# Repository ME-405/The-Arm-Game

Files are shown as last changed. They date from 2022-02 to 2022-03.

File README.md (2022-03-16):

# The Arm Game

Jacob Bograd, Nicholas De Simone, Horacio Albarran

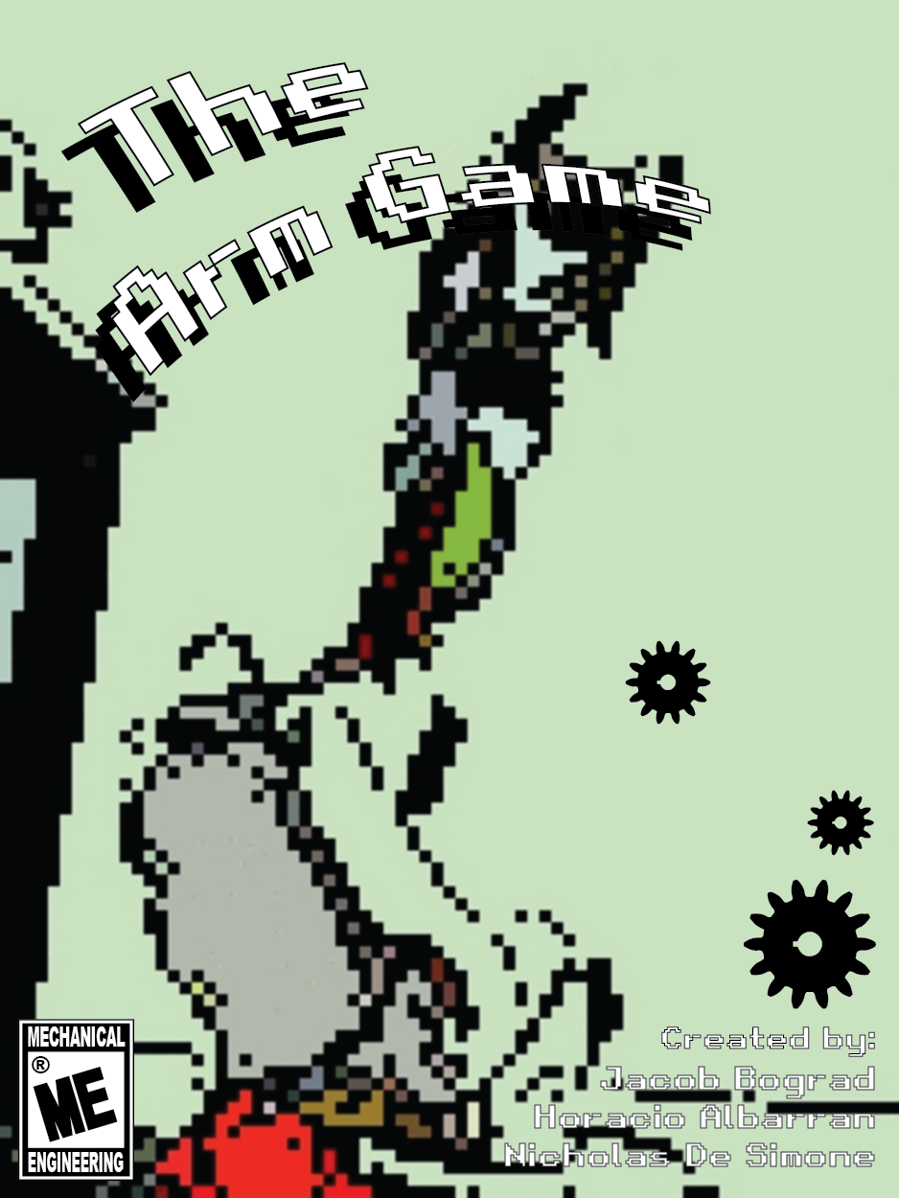
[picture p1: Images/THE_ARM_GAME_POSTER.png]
Poster


## Introduction

Our 3D-printed robotic arm is manipulated using a game controller, where the goal in using the arm is to grab a ping-pong ball and drop it through the "catching tables". The game controller communicates to the host computer over a library obtained through GitHub, and the PC interprets the controller inputs as desired end effector locations and sends them to a l476RG Nucleo. The Nucleo reads the given input arguments as x,y, and z-coordinates and transforms them into respective motor PWM values, which correspond to necessary angular positions for the servos. The Nucleo also sends the DC motor's encoder values back to the computer. All of the calculations are handled on the computer side, such that the Nucleo only sets PWM values for the respective motor and/or servos in order to get to the specified position for the claw at the end of the robotic arm. 

## Demonstration Video
The following video shows the functioning mechanism: 

https://user-images.githubusercontent.com/97562028/157779387-043f62d6-f68d-46a5-b4d3-32e55e5b0366.mp4

## Documentation and Software Design

There are ten .py files for the micro-controller side of the controller program. Such files allow for closed loop control of the used motor as well as providing with the required calculations in order to operate the arm, elbow, and clamping mechanism of the links.  
On the other hand, there is one required file on the computer side in order to open the console for the game controller to be used and provide with the desired x,y, and z-coordinates of the desired point in space where the claw must be located in order to grab the desired object, in this case, a ping-pong ball.
For further information, please refer to the following link for any documentation regarding "The Arm Game" project:

https://me-405.github.io/The-Arm-Game/

## Wiring Key
### Power
Red electrical Tape - 12V Motor \
Yellow electrical Tape - 7V Servo \
Green Electrical Tape  - 5V MicroServo \
Blue with Green - GND \
Black with Yellow - 7V

### Data
White - Servo0 \
Blue - Servo1 \
Black - Servo2\
Yellow - Servo3

### Data Nucleo Pins
PA5 - Servo0 \
PA6 - Servo1 \
PA7 - Servo2\
PC7 - Servo3

# Bill of materials

| Qty. | Part | Source | Est. Cost |
|:----:|:---|:---|:---:|
|  1 | Pittperson Gearmotors | ME405 Tub | - |
|  1 | l476RG Nucleo with Shoe | ME405 Tub | - |
|  2 | MG996R Servos[Package] | Amazon | 26.99 |
|  2 | SG90 Micro Servo [Package] | Amazon | 10.69 |
|  1 | Arms, Base, & Waist [3-D printed] | Bonderson's Building  | - |
|  1 | Game Controller [PS5 controller] | Jacob's Toolbox | 59.99 |
|  1 | Gear | 3-D printed | - |
| 10+  | Assorted metric bolt and nuts | Ace Hardware | - |
|  1 | Ping-Pong ball | Found | - |

# Gallery
## System Assembly
The following images show an overview of the arm mechanism:

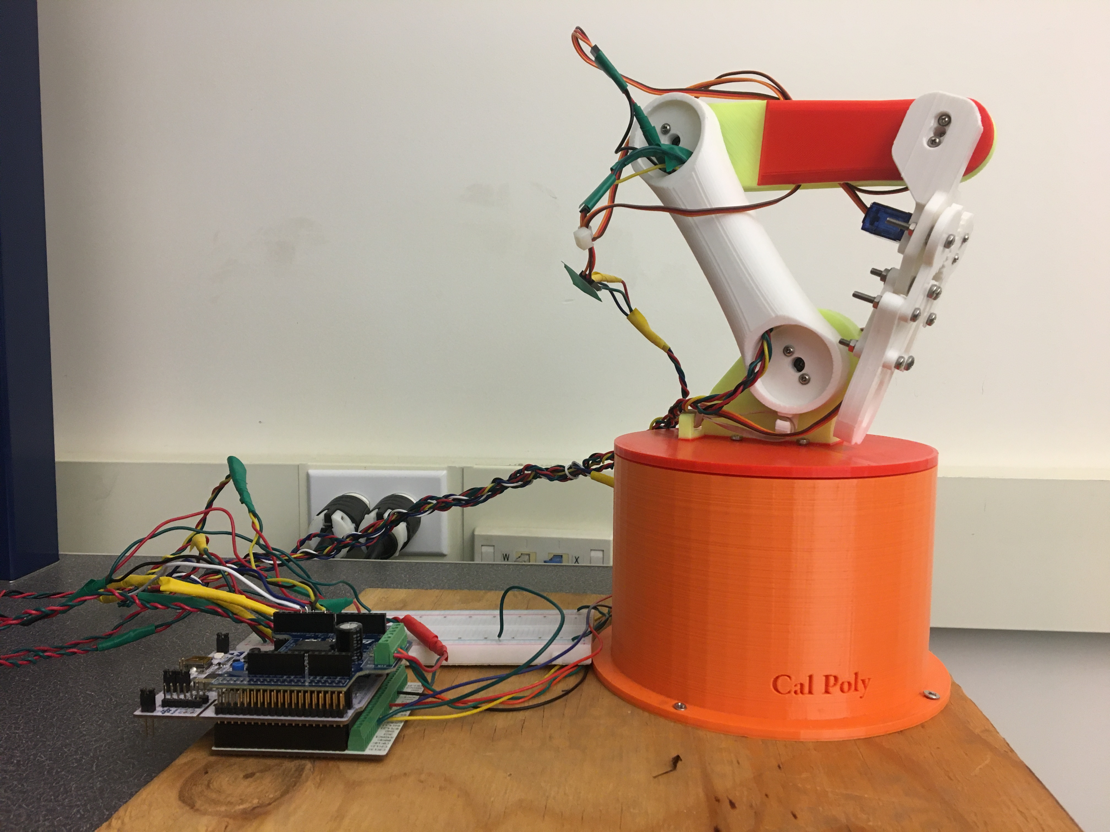
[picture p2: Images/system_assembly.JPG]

Figure 1: Overall system assembly. Complete arm mechanism shown to the right and microcontroller stack to the left. 

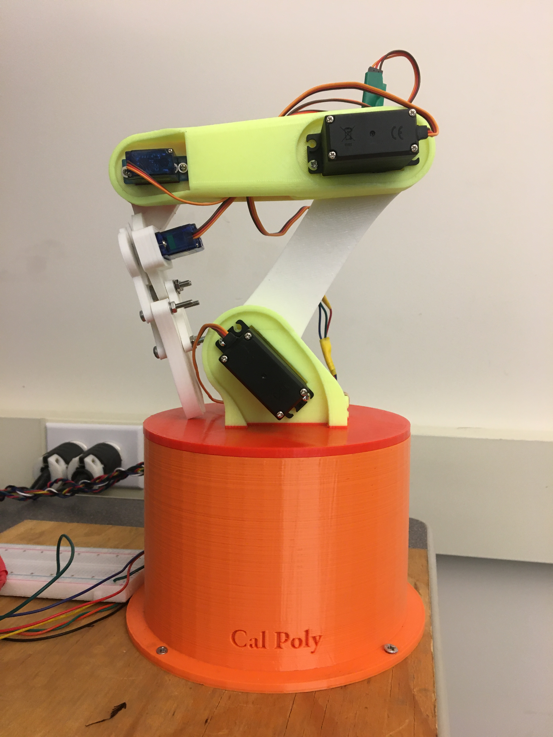
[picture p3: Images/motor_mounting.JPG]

Figure 2: Servo locations. 

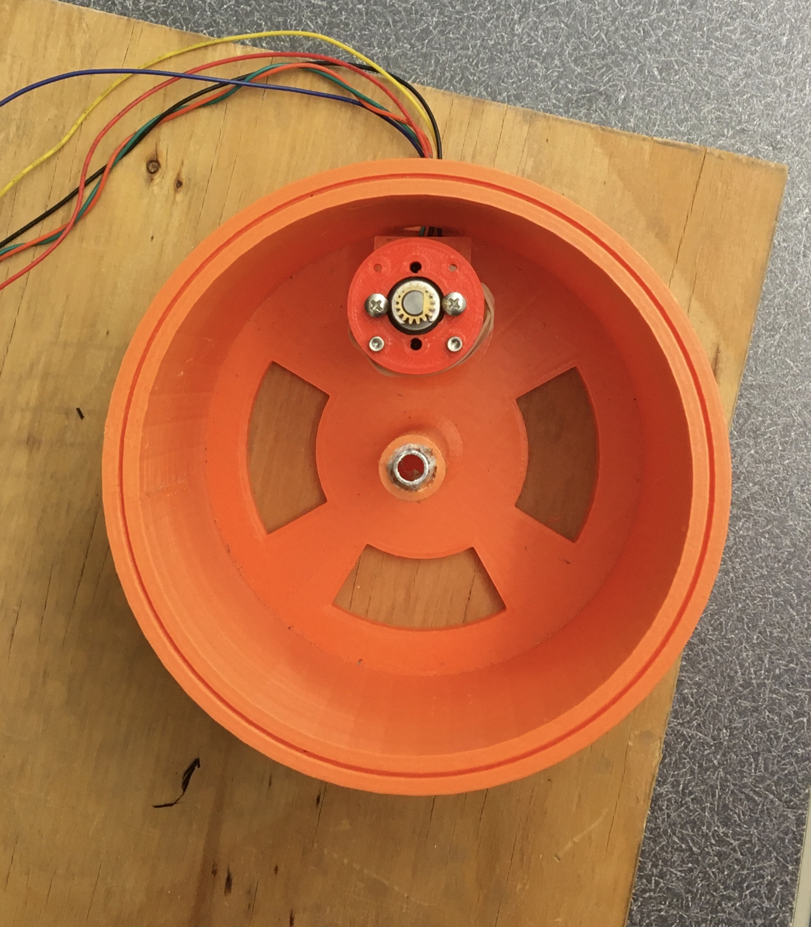
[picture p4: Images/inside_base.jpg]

Figure 3: Open-view of the base. Note (1) the internal vertically-mounted DC-motor, which mates to the waist's gear with a 7:1 gear ratio, and (2) the center-most shaft for mounting of the arm/waist assemblies to the base.

## Catching Table Sketch
The following model was constructed to be able to catch the ping-pong ball in an effective manner.
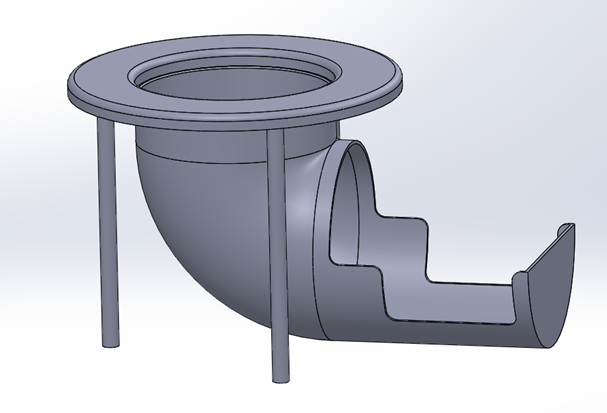
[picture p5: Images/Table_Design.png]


Figure 4: Model used for the Table hardware.

# Testing
System testing allowed us to observe physical constraints of the assembly and control them accordingly.
To begin, each component of the systems was tested individually (i.e. unique PWM signals were sent to each motor to ensure they behaved appropriately). 
An important component to testing became linkage alignment; we fixed the printed arms to the servo end effectors at strategic starting positions, such that each 
0-180 degree servo position produces desirable arm orientations.

We would like to note that communicating to a second terminal through the upper-most UART port on the microcontroller stack was a helpful feature in testing, as it allowed
for viewable debug statements from the Nucleo while busy sending actuation locations over its bottom-most USB-VCP port.
The mechanism did ultimately have undesirable behavior, which may be observed at length in the "Recommendations" section.

## Recommendations
It is important to note that, in our attempt to compute linkage angles according to a desired end effector location, our use of inverse kinematics control sometimes
produced unfavorable singularities in the arm's motion. Likely, our source of error stemmed from our application of a 2 degree-of-freedom, 2-link inverse kinematic
model to our controller, whereas, in practice, our robot arm has 3 degrees-of-freedom (not accounting for the gripper's pitch or close, as these were not included in our 
defined end effector location, i.e. the "end effector location" refers to the gripper wrist). Subsequent research into this error has suggested that the computation of 
linkage angles from an inputted end effector location may result in two unique orientations of the robot arm- either in the "elbow up" or "elbow down" configuration- at 
times producing undesired behavior. For example, when transistioning between specific points in space, the arm underwent rapid transition from "elbow up" to 
"elbow down", sometimes crashing the bot into the table or other times producing large inertial moments on the gripper assembly, causing it to snap at the end of its motion.
Possible solutions may include (1) proper consideration of and selection between the two unique orientation solutions found by our motor controller/kinematic solver scripts,
or (2) implementation of alternative controller methods, such as the Newton Raphson. The Newton Method may be more suited for our system because the arm has more than two DOF's.

We also found limits on the arms actuation in the radial direction due to insufficient fixturing/support at the base of the arm. Resultant undesired behavior included the arm
"jumping off" its orange base when actuating at a large radial distance (close to the length of both arms extended horizontally). Possible solutions include (1) fixing the
gear (currently attached on the undermost surface of the revolving waist) to both the orange base and the revolving waist, or (2) attaching physical masses to the
waist to counteract force moments when actuating in the downward direction.

It would also be recommended to obtain servos with higher output torque, as the 7V servos had difficulty sustaining the mechanism's weight. The microservos were able to
control gripper pitch and close without issue.

## Structural Components
Please refer to the following link for the 3D-printed structual components:

https://github.com/ME-405/The-Arm-Game/tree/main/Hardware_Components

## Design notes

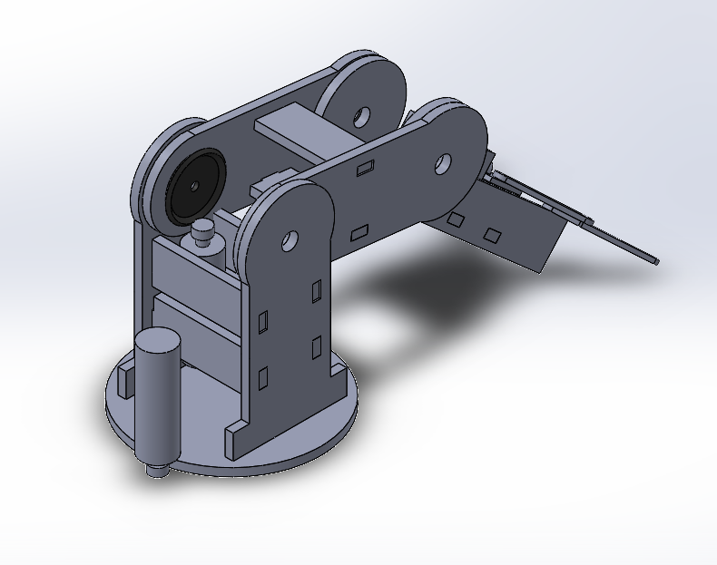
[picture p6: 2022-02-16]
docs/rough_model_back.png

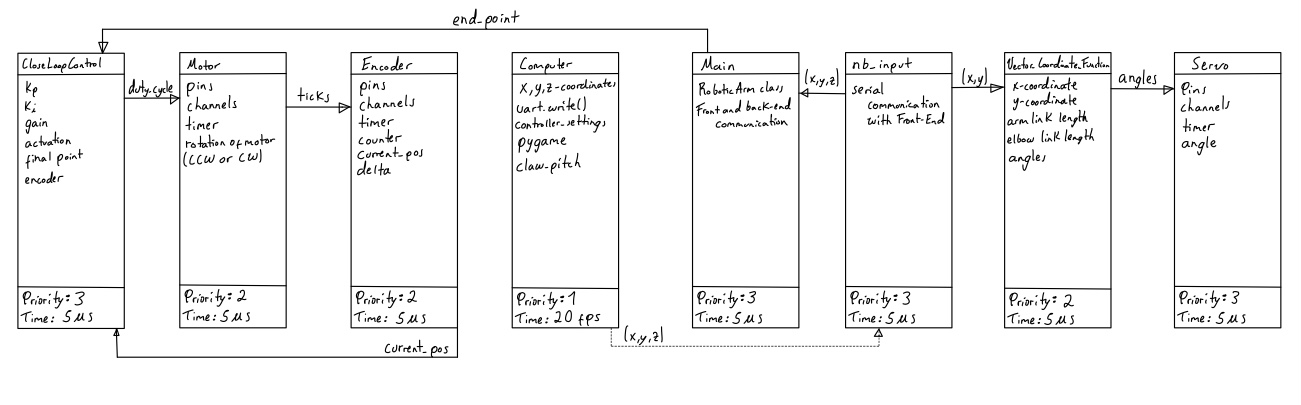
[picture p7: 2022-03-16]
docs/Task_Diagram.png

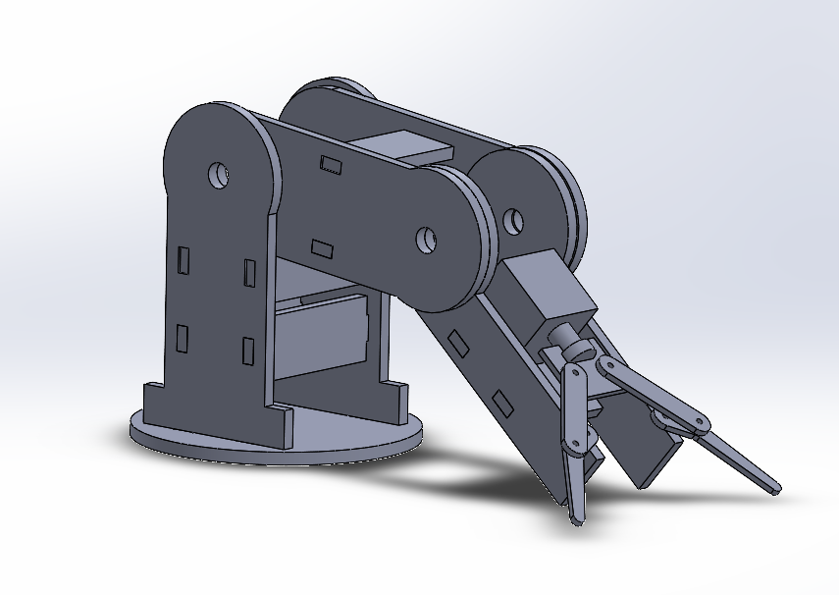
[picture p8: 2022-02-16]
Images/rough model.png

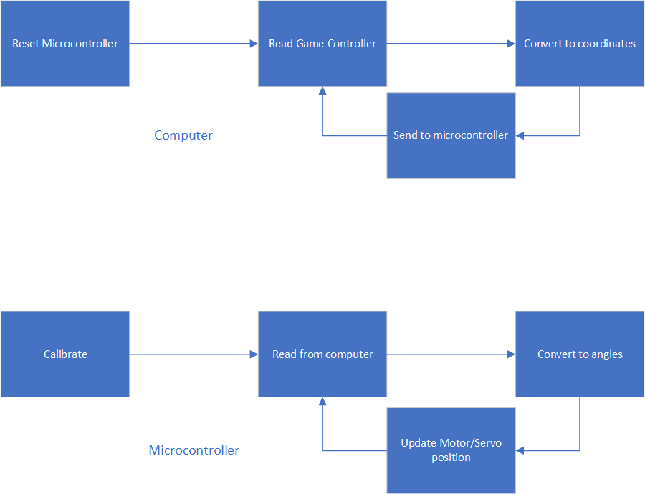
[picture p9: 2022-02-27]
Images/intinal_fsm.png

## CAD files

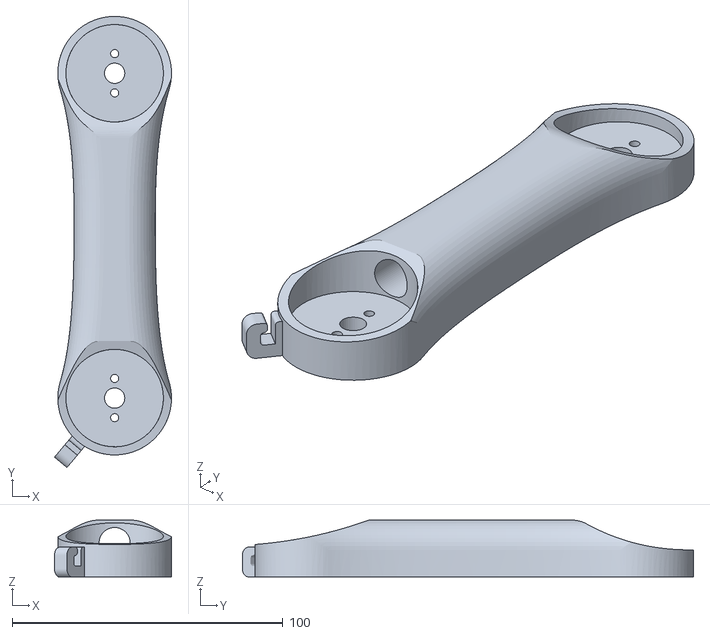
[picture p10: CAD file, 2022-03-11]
Hardware_Components/Arm 01.STL
43.2 x 166.7 x 21.0

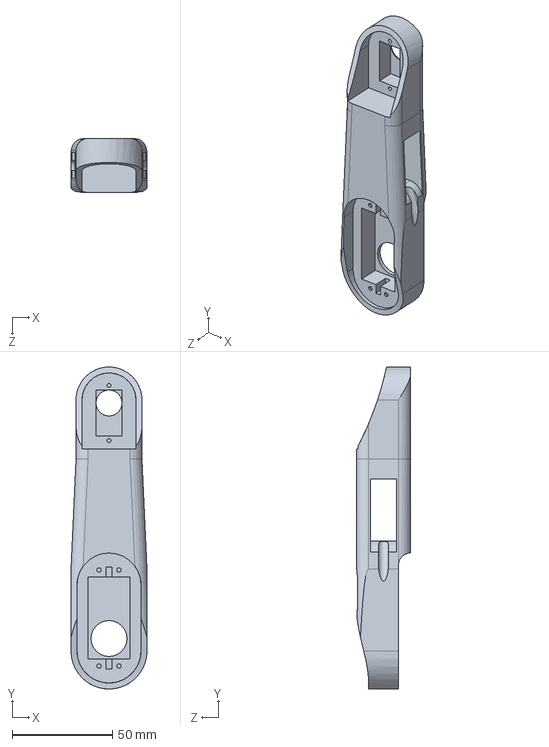
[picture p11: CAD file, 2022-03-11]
Hardware_Components/Arm 02 V4.SLDPRT
38.0 x 161.0 x 27.0 mm

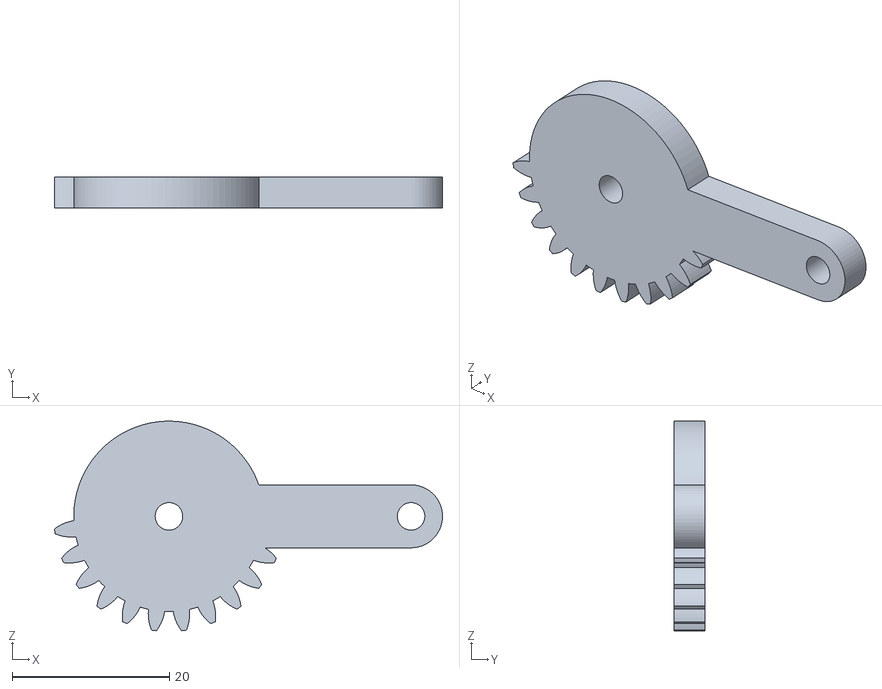
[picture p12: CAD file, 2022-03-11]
Hardware_Components/gear1.STL
49.3 x 4.00 x 26.6

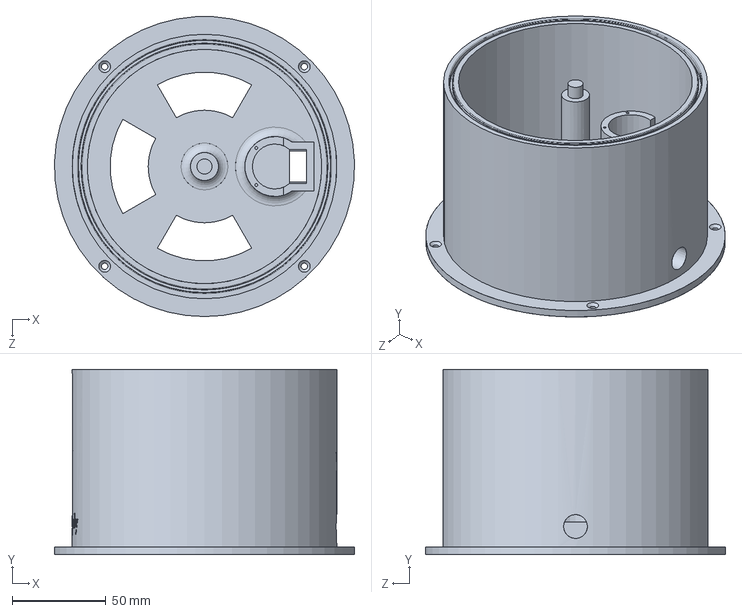
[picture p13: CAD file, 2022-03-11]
Hardware_Components/Base V3.SLDPRT
159.9 x 98.8 x 160.0 mm

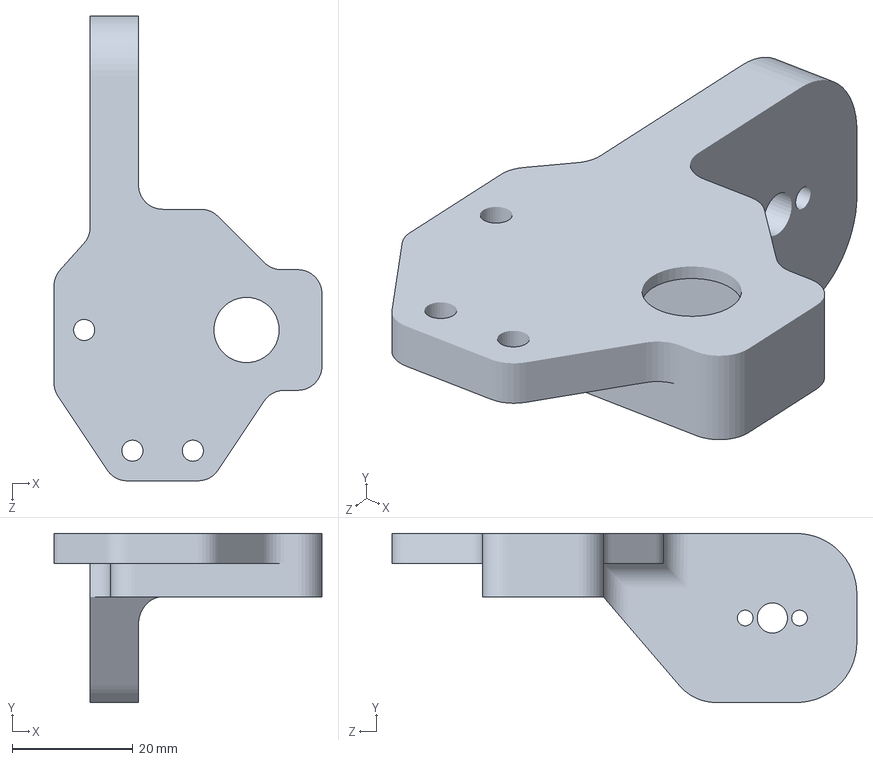
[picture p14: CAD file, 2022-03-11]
Hardware_Components/Gripper base.SLDPRT
44.4 x 28.0 x 77.0 mm

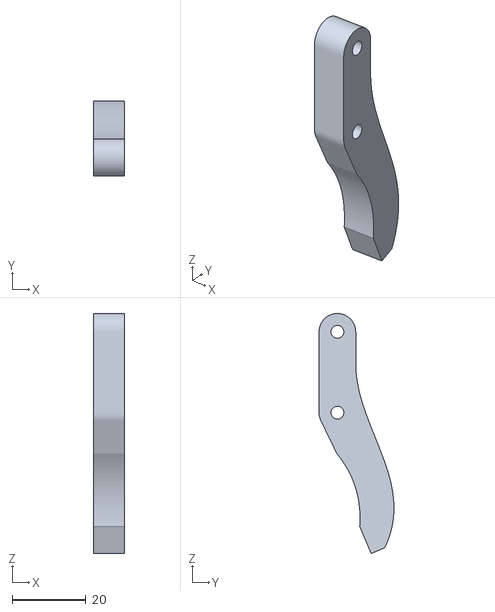
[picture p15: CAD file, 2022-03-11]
Hardware_Components/Gripper 1.STL
8.50 x 20.4 x 65.3

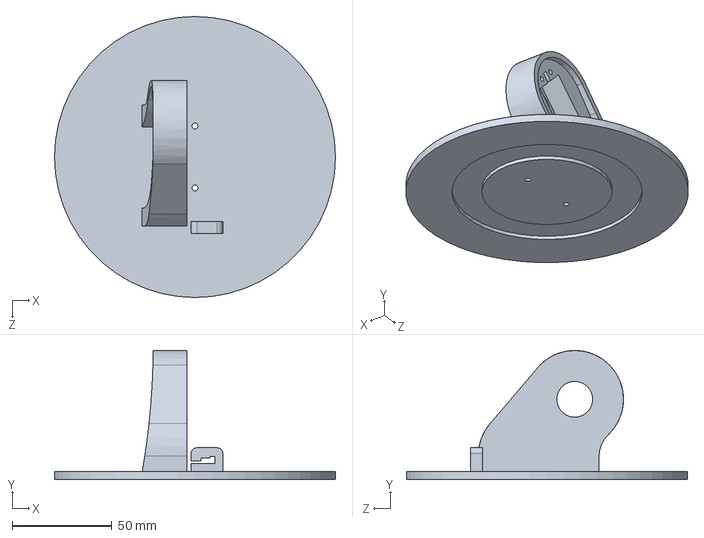
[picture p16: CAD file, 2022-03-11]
Hardware_Components/Waist V5.SLDPRT
141.0 x 64.8 x 141.0 mm

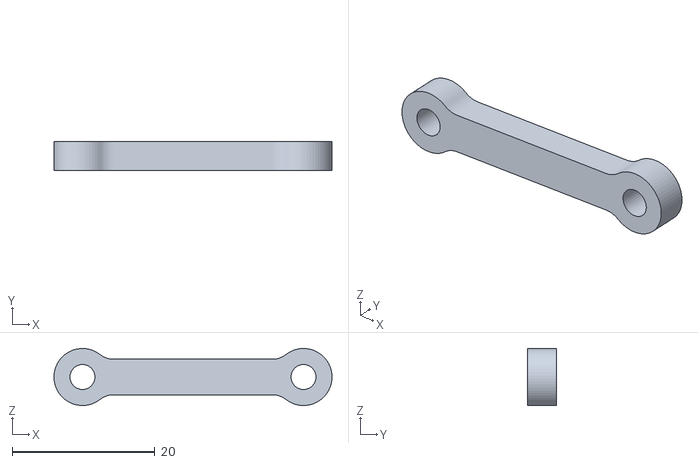
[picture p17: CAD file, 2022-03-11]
Hardware_Components/grip link 1.STL
39.0 x 4.00 x 8.00

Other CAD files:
Hardware_Components/gear2.STL

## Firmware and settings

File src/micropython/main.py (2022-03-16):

'''!
@file main.py
@details This is the main file for the Micropython side of this project. It contains the FSM that controls the whole system.
'''

#  Importing libraries and classes
from pyb import USB_VCP
from nb_input import NB_Input
from servo import Servo
from Motor import MotorDriver
from encoder import Encoder
from closedLoopControl import ClosedLoopController as ClosedLoop
from pyb import UART
from Vector_Coordinate_Function import ElArAngles
import pyb
import gc
import cotask
import task_share
import math

INPUTINTERVAL = 10

DEFAULTANGLE = 60  # the default angle


# Instantiated the objects for the servos


def main():
    '''!
    @breif This is the main function that the MCU runs  whenever it is restarted
    '''
    # start by creating a share and queue
    arm = RoboticArm()  # make a new robotic arm

    # I am not sure if the share and queue are needed
    share = task_share.Share('h', thread_protect=False, name="Share")
    queue = task_share.Queue('L', 16, thread_protect=False, overwrite=False,
                             name="Queue")
    per_val = 5
    read_task = cotask.Task(arm.read_uart, name='read', priority=1, period=per_val, profile=False, trace=False)
    calculate_task = cotask.Task(arm.calculate_parameters, name='calculate', priority=2, period=per_val, profile=False,
                                 trace=False)
    update_task = cotask.Task(arm.update_parameters, name='update', priority=2, period=per_val, profile=False,
                              trace=False)
    clc_task = cotask.Task(arm.clc.control_algorithm, name='clc', priority=3, period=per_val, profile=False,
                           trace=False)
    # append all the tasks to the task list
    read = arm.read_uart()
    calculate = arm.calculate_parameters()
    update = arm.update_parameters()
    clc = arm.clc.control_algorithm()
    cotask.task_list.append(read_task)
    cotask.task_list.append(calculate_task)
    cotask.task_list.append(update_task)
    cotask.task_list.append(clc_task)

    gc.collect()
    # run the garbage collector

    # run the scheduler
    print("hello Computer")
    while True:
        # next(read)
        # print("calculating")
        # next(calculate)
        # print("Updating")
        # next(update)
        # print("clc")
        # print(f"MCU DEBUG: error: {arm.clc.send_error}, actuation: {arm.clc.send_actuation}, current pos {arm.clc.encoder.current_pos}, final pos {arm.clc.final_point}")
        # for i in range(1, 10):
        # next(clc)
        # Everything above this is DEBUG
        cotask.task_list.pri_sched()  #Grab another cotask
    print("Look All Done")  # DEBUG, this will not happen


class RoboticArm:
    def __init__(self, uart_channel=2, baudrate=115200):
        '''!
        @brief TODO
        @details TODO
        @param uart_channel     This is the uart channel that we will be using for communication
        @param baudrate         This is the baudreate that we will be using for communication
        TODO update the doxygen from @param
        @param self.uart        This is the uart channel that we will be using for communication with the host machine
        @param self.clc         This is the close loop controller for the base
        @param self.command     This is the raw command taken from the host computer, it will be processed into angles and positions at a later date
        @param self.angles      This is a list that contains all of the angles for the servos to go to
        @param self.endpoint    This is the updated encoder endpoint for the base
        @param self.new_values  This is a boolean to determine if we need to update the parameters
        @param self.mail        This is a boolean to determine if we have new mail from the computer
        '''

        # Instantiated object for the encoder as well as timer,
        encoderPin1 = pyb.Pin(pyb.Pin.board.PB6)
        encoderPin2 = pyb.Pin(pyb.Pin.board.PB7)
        EncTimer1 = 4
        EncoderDriver = Encoder(encoderPin1, encoderPin2, EncTimer1, 1, 2)

        # Instantiated the objects for the motor
        motorEnable1 = pyb.Pin(pyb.Pin.board.PC1, pyb.Pin.IN, pyb.Pin.PULL_UP)
        motor1Pin1 = pyb.Pin(pyb.Pin.board.PA0, pyb.Pin.OUT_PP)
        motor1Pin2 = pyb.Pin(pyb.Pin.board.PA1, pyb.Pin.OUT_PP)
        motorTimer = pyb.Timer(5, freq=20000)
        Motor = MotorDriver(motorEnable1, motor1Pin1, motor1Pin2, motorTimer, 1, 2)

        # Conditionals for the USB coms
        self.serial_stream = USB_VCP()
        self.nb_in = NB_Input(self.serial_stream, echo=False)

        # now setup all of the class variables


        self.clc = ClosedLoop(EncoderDriver, Motor)  # make a new closed loop controller
        # self.command = [1, 0.1, 0.1, 100, 60]  #DEBUG
        self.command = None  # set the command to nothing

        # make the 4 servo objects, the pins are hard-coded
        # The setup for the pins might not be correct
        self.servo0 = Servo(pyb.Pin(pyb.Pin.board.PA5), 2, 1)  # The lower arm servo
        self.servo1 = Servo(pyb.Pin(pyb.Pin.board.PA6), 3, 1)  # The middle arm servo
        self.servo2 = Servo(pyb.Pin(pyb.Pin.board.PA7), 3, 2)  # The upper arm servo
        self.servo3 = Servo(pyb.Pin(pyb.Pin.board.PC7), 8, 2)  # The claw servo
        self.angles = [DEFAULTANGLE, DEFAULTANGLE, DEFAULTANGLE, DEFAULTANGLE]  # set all of the angles to default
        self.endpoint = DEFAULTANGLE  # Set the default endpoint
        self.new_values = False  # we do not have any new values to read
        # self.mail = True # DEBUG
        self.mail = False  # we do not have any mail from the computer
        self.VCF = ElArAngles()  # make the Vector Coordinate Function
        self.conversion_factor = 319  # The conversion factor from angle to encoder ticks

    # TODO ADD DOXY
    def read_uart(self):
        while True:
            if self.nb_in.any():
                # if True:
                # if self.uart.any():  # check if there is something in the pipeline
                command_string = self.nb_in.get().split(',')  # read in the command and split on ,
                self.command = [float(coordinate) for coordinate in command_string]  # convert the string list to float
                print("ACK")  # we acknowledge
                self.mail = True  # we have some mail to sort through
            else:
                # print("No Mail") # DEBUG
                self.mail = False  # we have no new mail
            yield 0  # let another task have its turn in the spotlight

    # TODO ADD DOXY
    def calculate_parameters(self):
        # The format is X,Y,Z,CLAW PITCH, CLAW CLOSE
        while True:
            if self.mail:  # only calculate parameters if there is something that we need to do
                #  Get the base angle
                #  Ange = arctan(y/x)
                radians = math.atan2(self.command[1], self.command[0])  # get the angle in radians
                self.endpoint = radians * self.conversion_factor * 180 / math.pi  # convert the angle to encoder ticks
                # radius = math.sqrt(self.command[0]**2 + self.command[1]**2)
                self.VCF.set_angles(self.command[1], self.command[2])  # update the VCF with the new angles
                self.VCF.run()  # Have the VCF calculate the new angles

                # Get the angles for the 4 servos
                self.angles[0] = self.VCF.tetha1
                self.angles[1] = 180 - (self.VCF.tetha2 + 90)  # The servo is backwards
                # print(self.angles[1])  # DEBUG
                # The claw close and pitch are given as angles

                self.angles[2] = 180 - self.command[3]  # get the claw pitch value
                self.angles[3] = self.command[4]  # get the claw close value
                self.new_values = True
            yield 0  # send it back for another task to take over

    def update_parameters(self):
        while True:
            if self.new_values:
                # update the servo angles
                self.servo0.SetAngle(self.angles[0])
                self.servo1.SetAngle(self.angles[1])
                self.servo2.SetAngle(self.angles[2])
                self.servo3.SetAngle(self.angles[3])
                # update the base endpoint
                self.clc.final_point = self.endpoint
                # print(f"angle0 {self.angles[0]} angle1 {self.angles[1]} angle2 {self.angles[2]} angle3 {self.angles[3]}")
            else:
                manual_breathing = 1  # you are now manually breathing
            yield 0  # let another function have its turn

    # this is just a simple pass-through to run the clc update
    def clc_passthrough(self):
        self.clc.control_algorithm()

    def zero_encoder(self):
        '''!
        @brief This resets the encoder value in the clc to 0, for use in case of a failure and without a hardware reset
        '''
        self.clc.encoder.zero()


# Dunder method to run the function when the name of the file is main,
if __name__ == '__main__':
    main()

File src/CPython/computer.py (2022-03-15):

import pygame
import serial
import time


# constants
XLIMIT = 4.65 * 2
YLIMIT = 4.65 * 2
ZLIMIT = 4.65 * 2
debug = False
ACK = True
try:
    uart_to_micro = serial.Serial(port='COM5', baudrate=115200, timeout=0)
    # reset the Microcontroller
    uart_to_micro.write(b'\x03')  # send Ctr+C
    time.sleep(0.5)  # sleep for half a second
    uart_to_micro.write(b'\x04')  # send Ctrl+D
    uart_to_micro.reset_input_buffer()
    uart_to_micro.reset_output_buffer()
    time.sleep(5)
    debug = False
except serial.serialutil.SerialException:
    print("INVALID UART, ENTERING DEBUGGING MODE")
    debug = True

# TODO CLEAN UP BELOW

# Define some colors.
BLACK = pygame.Color('black')
WHITE = pygame.Color('white')


# This is a simple class that will help us print to the screen.
# It has nothing to do with the joysticks, just outputting the
# information.
class TextPrint(object):
    def __init__(self):
        self.reset()
        self.font = pygame.font.Font(None, 20)

    def tprint(self, screen, textString):
        textBitmap = self.font.render(textString, True, BLACK)
        screen.blit(textBitmap, (self.x, self.y))
        self.y += self.line_height

    def reset(self):
        self.x = 10
        self.y = 10
        self.line_height = 15

    def indent(self):
        self.x += 10

    def unindent(self):
        self.x -= 10


pygame.init()

# Set the width and height of the screen (width, height).
screen = pygame.display.set_mode((500, 700))

pygame.display.set_caption("The-Arm-Game")

# Loop until the user clicks the close button.
done = False

# Used to manage how fast the screen updates.
clock = pygame.time.Clock()

# Initialize the joysticks.
pygame.joystick.init()

# Get ready to print.
textPrint = TextPrint()

# intinalize the starting variables
Xaxis = 0
Yaxis = 4.6
Zaxis = 4.6  # start off as zero
to_print = "Nothing Yet"
previous_to_print = None
# -------- Main Program Loop -----------
while not done:
    #
    # EVENT PROCESSING STEP
    #
    # Possible joystick actions: JOYAXISMOTION, JOYBALLMOTION, JOYBUTTONDOWN,
    # JOYBUTTONUP, JOYHATMOTION
    for event in pygame.event.get():  # User did something.
        if event.type == pygame.QUIT:  # If user clicked close.
            done = True  # Flag that we are done so we exit this loop.

    #
    # DRAWING STEP
    #
    # First, clear the screen to white. Don't put other drawing commands
    # above this, or they will be erased with this command.
    screen.fill(WHITE)
    textPrint.reset()
    # Get count of joysticks.  # DEBUG
    joystick_count = pygame.joystick.get_count()  # DEBUG
    textPrint.tprint(screen, "Number of joysticks: {}".format(joystick_count))  # DEBUG
    textPrint.indent()  # DEBUG

    # For each joystick:
    for i in range(joystick_count):
        joystick = pygame.joystick.Joystick(i)
        joystick.init()

        try:
            jid = joystick.get_instance_id()
        except AttributeError:
            # get_instance_id() is an SDL2 method
            jid = joystick.get_id()
        textPrint.tprint(screen, "Joystick {}".format(jid))
        textPrint.indent()

        # Get the name from the OS for the controller/joystick.
        name = joystick.get_name()
        textPrint.tprint(screen, "Joystick name: {}".format(name))

        try:
            guid = joystick.get_guid()
        except AttributeError:
            # get_guid() is an SDL2 method
            pass
        else:
            textPrint.tprint(screen, "GUID: {}".format(guid))

        # Usually axis run in pairs, up/down for one, and left/right for
        # the other.
        axes = joystick.get_numaxes()
        textPrint.tprint(screen, "Number of axes: {}".format(axes))
        textPrint.indent()

        for i in range(axes):
            axis = round(joystick.get_axis(i), 1)
            textPrint.tprint(screen, "Axis {} value: {:>6.3f}".format(i, axis))
        textPrint.unindent()

        ########################################################################
        # NOW WE START THE ME405 SECTION
        # Format of the packet is [X, Y, Z, CLAW PITCH, CLAW CLOSE]
        # NOTE All joystick values are rounded to ONE decimal point due to joystick drift
        # R2 (Axis 5) is the claw
        claw_close = round((joystick.get_axis(5) + 1) * 90, 0)  # take the joystick input, make it from 0 - 2 then
        if claw_close > 45:
            claw_close = 45
        elif claw_close < 0:
            claw_close = 0

        # convert to angle
        claw_pitch = round((joystick.get_axis(4) + 1) * 90, 0)  # same as above
        if claw_pitch < 0:
            claw_pitch = 0
        elif claw_pitch > 90:
            claw_pitch = 90
        textPrint.tprint(screen, "Claw Pitch {}".format(claw_pitch))
        textPrint.tprint(screen, "Claw Angle {}".format(claw_close))
        buttons = joystick.get_numbuttons()
        textPrint.tprint(screen, "Number of buttons: {}".format(buttons))
        textPrint.indent()

        for i in range(buttons):
            button = joystick.get_button(i)
            textPrint.tprint(screen,
                             "Button {:>2} value: {}".format(i, button))
        textPrint.unindent()
        # Left Stick X (Axis 0) is X axis
        Xaxis = (joystick.get_button(14) * 0.1 + Xaxis)
        Xaxis = Xaxis - (joystick.get_button(13) * 0.1)

        #Xaxis = round(joystick.get_axis(0) + Xaxis, 1)

        # Left Stick Y (Axis 0) is Y axis
        Yaxis = (joystick.get_button(11) * 0.1) + Yaxis
        Yaxis = Yaxis - (joystick.get_button(12) * 0.1)
        #Yaxis = round((-1 * joystick.get_axis(1)) + Yaxis, 1)  # Negative 1 because joystick is backwards
        Xaxis = round(Xaxis, 3)
        Yaxis = round(Yaxis, 3)
        # L2 (Axis 4) is Z axis
        # 0 is ground 2 is max vertical
        Zaxis = round(((-1 * joystick.get_axis(3)) * 0.1) + Zaxis, 1)  # Negative 1 because joystick is backwards

        # check that the axis are not at their limit
        '''
        if Xaxis > XLIMIT:
            Xaxis = XLIMIT
        if Yaxis > YLIMIT:
            Yaxis = YLIMIT
        if Zaxis > ZLIMIT:
            Zaxis = ZLIMIT
        if Xaxis < -2.1:
            Xaxis = -2.1
        if Yaxis < -8:
            Yaxis = -8
            '''
        if Zaxis == 0:
            Zaxis = 0.000001
        if Xaxis == 0:  # hardcode to never be at 0 to avoid division by zero
            Xaxis = 0.000001
        if Yaxis == 0:
            Yaxis = 0.000001
        if Zaxis == 0:
            Zaxis = 0.000001

        textPrint.tprint(screen, "Coordinates: {},{},{}".format(Xaxis, Yaxis, Zaxis))
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

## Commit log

2022-02-16 Adding Motor URL
2022-02-22 BOM update
2022-03-01 Updated the UART stuff
2022-03-05 Added servo pins and math
2022-03-11 Read Me Update
    [Arm 01.STL, Arm 02 V4.SLDPRT, Base V3.SLDPRT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]
2022-03-15 Delete sections
    Calibration and Parts sections were deleted
